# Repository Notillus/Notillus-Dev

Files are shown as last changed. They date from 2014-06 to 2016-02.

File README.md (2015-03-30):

Notillus
========

Repositorio de desarrollo de la Notillus, impresora originalmente inspirada en la Tantillus de https://github.com/Intrinsically-Sublime/Tantillus por su tamaño y portabilidad.

La Notillus ahora lleva el tanga extruder de coleta http://www.thingiverse.com/thing:742584

Los archivos de desarrollo de la Tantillus-Mks ahora estan en: 
https://github.com/darkjavi/Tantillus-MKS

Usando git:

Instrucciones para linux:

-Instalar:

	sudo apt-get install git

-Configurar

	git config --global user.name "TuNombre"

	git config --global user.email "tu@email.com"

-Primer clonado del repo:

	cd carpeta/donde/quieres/descargar

	git clone https://github.com/darkjavi/Notillus.git

-Actualizando el repo:

	cd carpeta/del/repo

	git pull

-Despues de haber modificado cosas en los ficheros:

	cd carpeta/del/repo

	git add .       (añade todos los archivos nuevos)

	git commit -a	(se abrira una ventana en la que obligatoriamente hay que escribir algo sobre los cambios hechos)

	git push origin (manda los cambios de vuelta a github, pedira nombre de usuario/pass)

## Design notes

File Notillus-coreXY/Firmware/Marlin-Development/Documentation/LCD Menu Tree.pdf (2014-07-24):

# Marlin LCD Menu Tree

Main Menu | Tune Menu | Move Menu
Info screen | Main | Prepare
Tune | Speed | Move 10mm | Move Menu
Prepare | Nozzle | Move 1mm | Move axis
Control | Nozzle2 | Move 0.1mm | Move X
Pause print | Nozzle3 | | Move Y
Resume print | Bed | | Move Z
Stop print | Fan speed | Temperature Menu | Extruder
Print from SD | Flow | Control
Change SD card | Babystep X | Nozzle
No SD card | Babystep Y | Nozzle2
Init. SD card | Babystep Z | Nozzle3
| Change filament | Bed
| | Fan speed
| | Autotemp
| Prepare Menu | \002 Min
| Main | \002 Max | Preheat PLA
| Autostart | \002 Fact | Temperature
| Disable steppers | PID-P | Fan speed
| Auto home | PID-I | Nozzle
| Preheat PLA | PID-D | Bed
| Preheat ABS | PID-C | Store memory
| Cooldown | Preheat PLA conf
| Switch power off | Preheat ABS conf | Preheat ABS
Switch power on | Temperature
Move axis | Fan speed
| Motion Menu | Nozzle
| Control | Bed
Control Menu | Z Offset | Store memory
Main | Accel
Temperature | Vxy-jerk
Motion | Vz-jerk
LCD contrast | Ve-jerk
Retract | Vmax x
Store memory | Vmax y
Load memory | Vmax z
Restore failsafe | Vmax e
| Vmin
| VTrav min
SD Card Menu | Amax x
Main | Amax y
Refresh | Amax z
filenames | Amax e
| A-retract
| Xsteps/mm
| Ysteps/mm
| Zsteps/mm
| Esteps/mm
| Endstop abort

Retract Menu
Control
AutoRetr.
Retract mm
Retract F
Hop mm
UnRet +mm
UnRet F

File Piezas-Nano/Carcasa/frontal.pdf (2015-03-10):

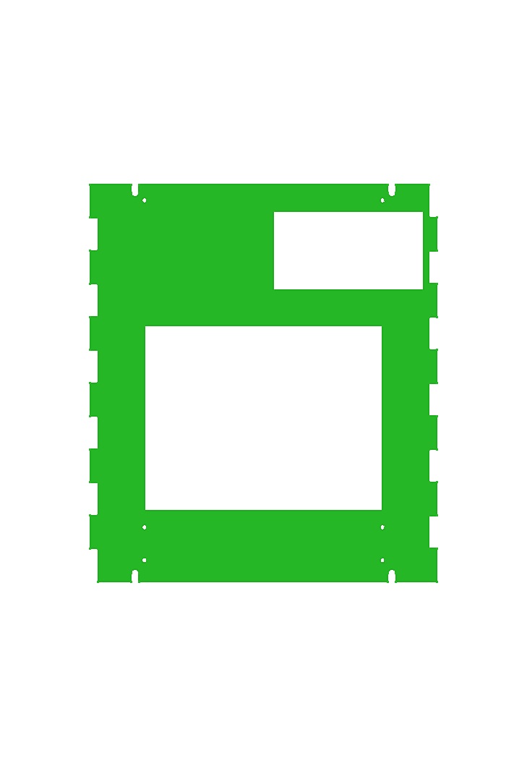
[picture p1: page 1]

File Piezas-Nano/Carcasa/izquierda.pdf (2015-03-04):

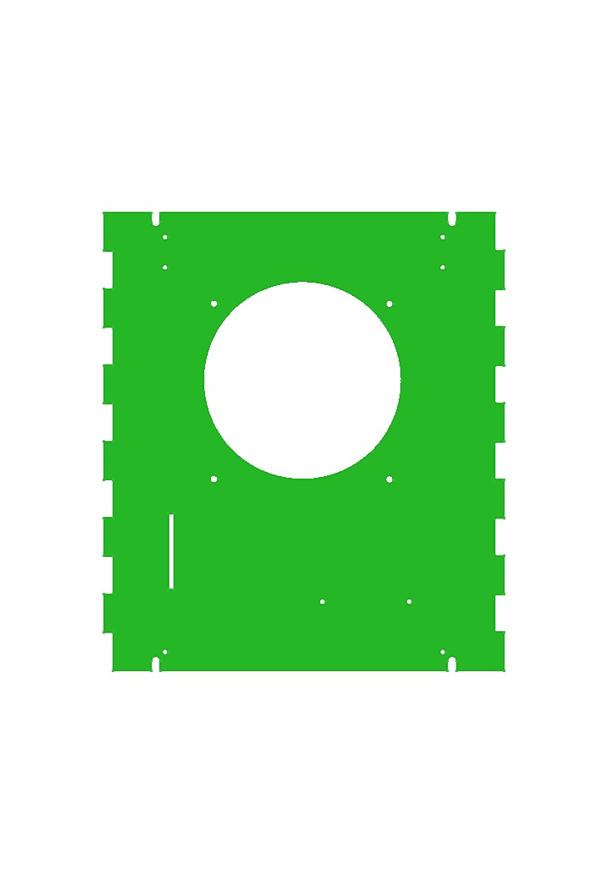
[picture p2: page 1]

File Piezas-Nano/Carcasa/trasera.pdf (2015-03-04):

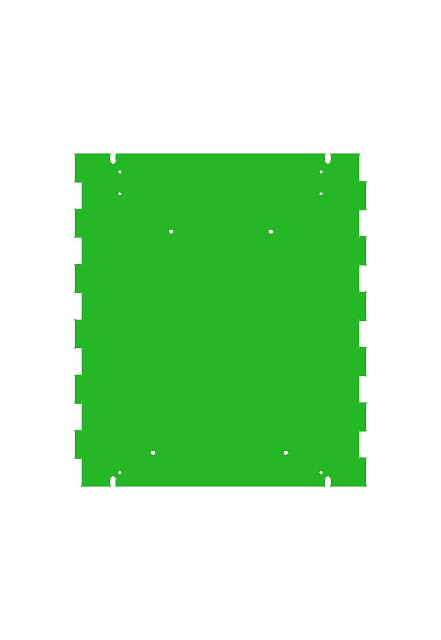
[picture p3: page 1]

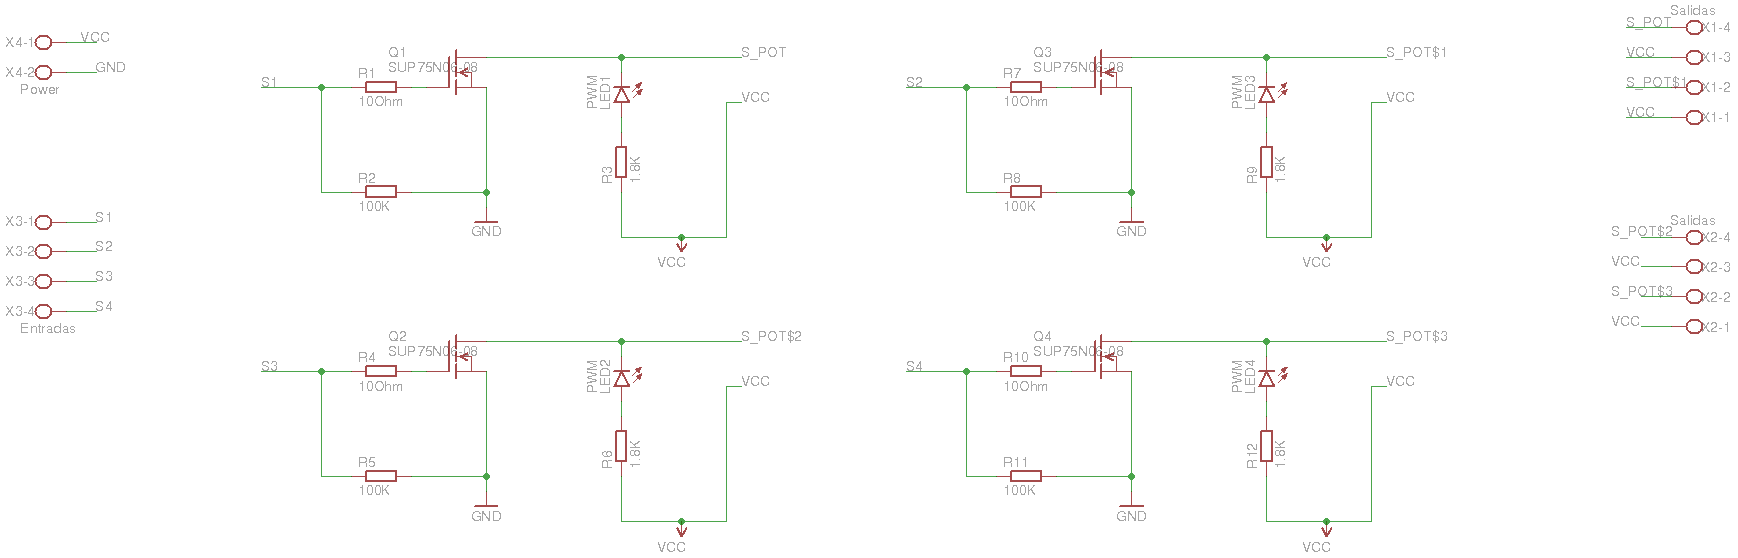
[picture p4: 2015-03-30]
Electronica/ExpansionBoard_sch.png

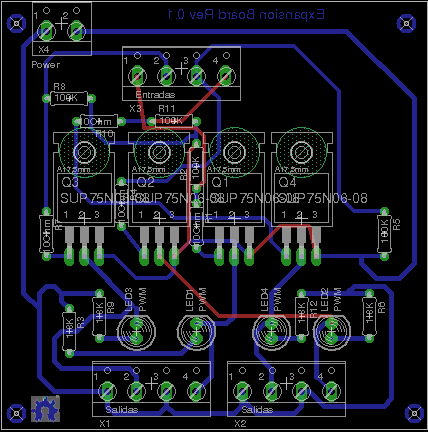
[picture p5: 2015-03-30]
Electronica/ExpansionBoard.png

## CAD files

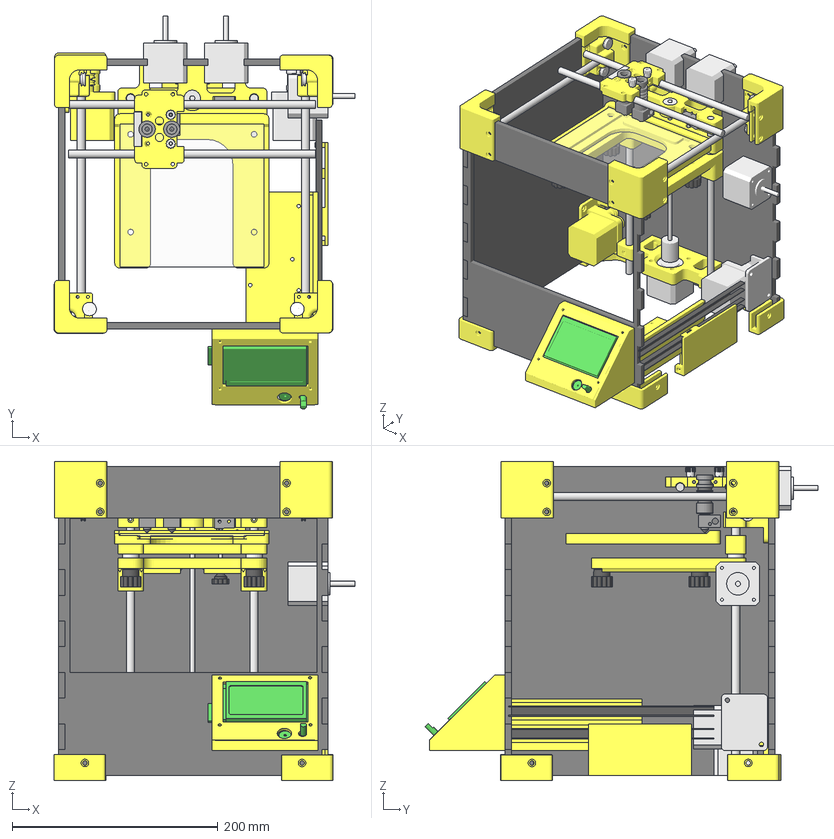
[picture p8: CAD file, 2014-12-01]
Piezas-Javi/Notillus/Ensamblaje1.1.fcstd
292.4 x 382.0 x 310.0 mm
Clone of Pieza base001
Clone of Pieza base003
Varilla8mm002
Clone of Chamfer009
acoplador001
Varilla5mm001
Prism002
PlataformaCierre001
Clone of Chamfer006
enstopz003
LM8UUL002
Nivelador002
625ZZ001
Varilla8mm003
Clone of KnobM007
LM8UUL003
NEMA019
Clone of Chamfer008
Clone of Chamfer007
Cristal001
Plataforna001
Motor
corredera_movil003
corredera_movil004
Completo001
DisplayFull
EsquinaInferior
EsquinaInferior001
EsquinaInferior002
EsquinaInferior003
EsquinaSuperior
EsquinaSuperior001
EsquinaSuperior002
EsquinaSuperior003
JheadMk010
JheadMk011
Knob-ccw002
Knob-cw002
varillax003
varillax002
Fusion001 (Mirror #2)
Fusion004 (Mirror #4)
Fusion002 (Mirror #5)
Cylinder013 (Mirror #6)
Fusion003 (Mirror #7)
Pocket011 (Mirror #9)
Pad027 (Mirror #9)
MotorA
MotorB
NEMA021
NEMA022
NEMA023
compartimento

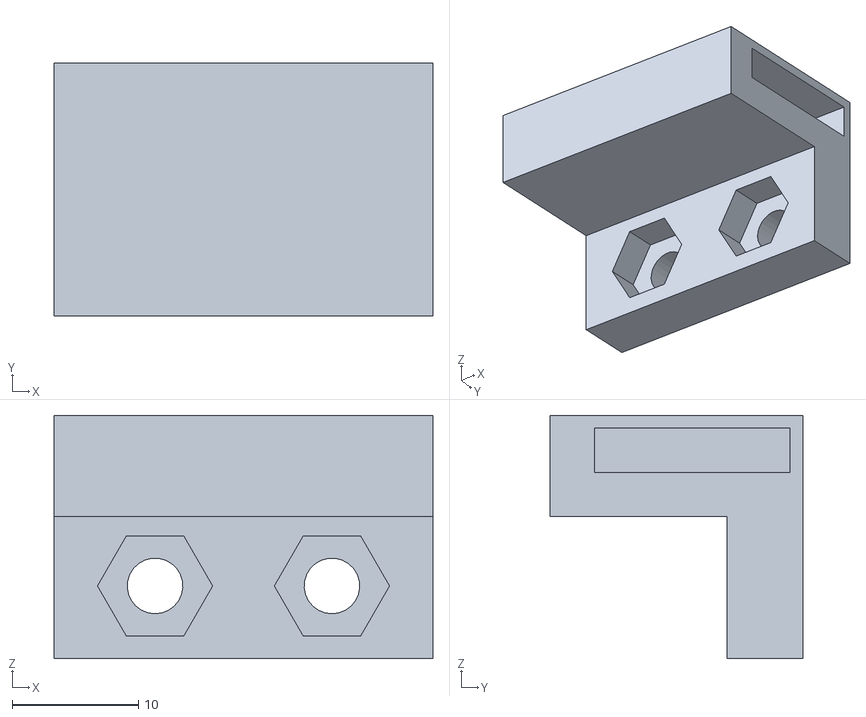
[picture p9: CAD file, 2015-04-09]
Notillus-coreXY/Botiquin/Cierre.stl
30.0 x 20.0 x 19.2

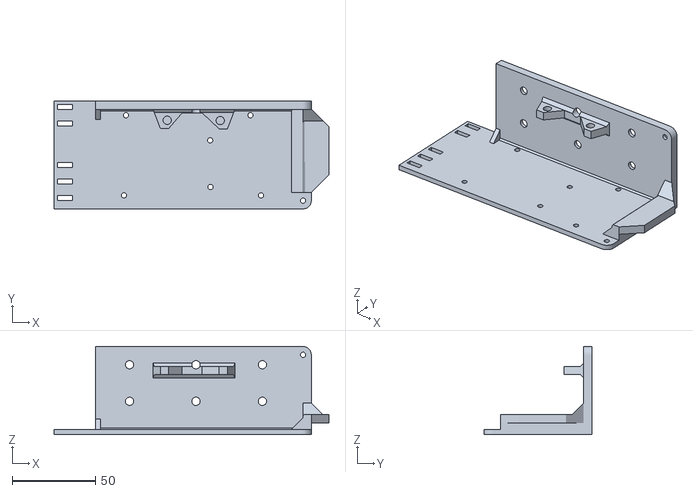
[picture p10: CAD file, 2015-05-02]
Notillus-coreXY/Cajon de Electronica/cajon_electronica.stl
165.6 x 65.0 x 53.0

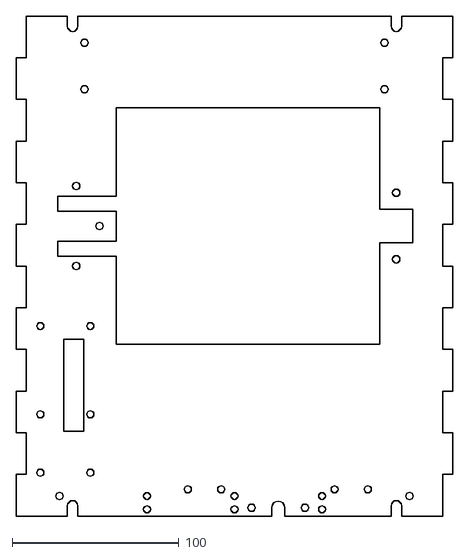
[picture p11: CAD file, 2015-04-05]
Notillus-coreXY/Carcasa/CorteLaser/lateral-izq.dxf
262.0 x 300.0

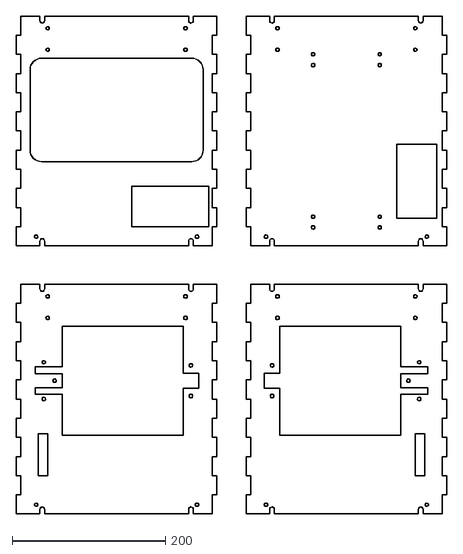
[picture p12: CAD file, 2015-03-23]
Notillus-coreXY/Carcasa/CorteLaser/Pruebas/test.dxf
562.0 x 650.0

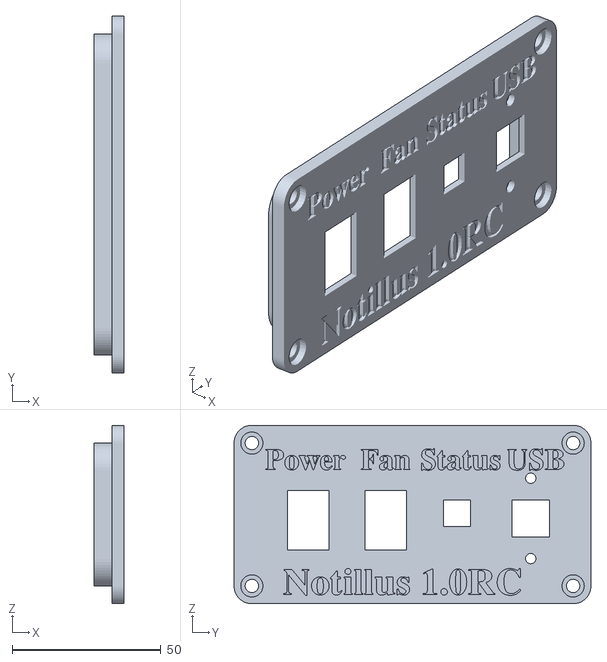
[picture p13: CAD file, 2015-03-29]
Notillus-coreXY/Carcasa/Panel-Interruptores/panel.stl
10.0 x 120.0 x 60.0

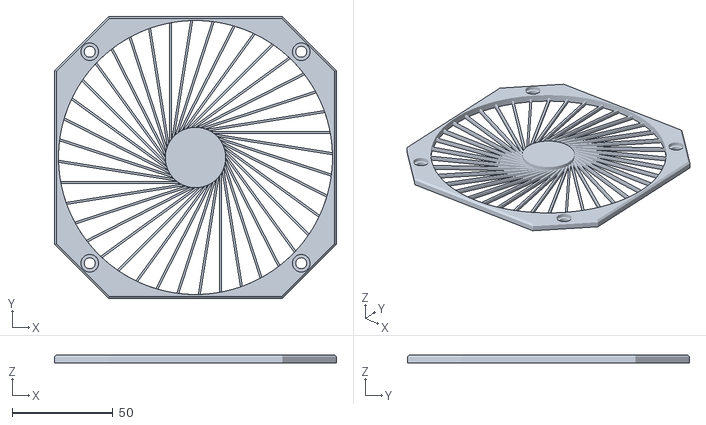
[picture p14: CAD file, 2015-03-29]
Notillus-coreXY/Carcasa/Puerta-Ventis/protector-ventis.stl
140.0 x 140.0 x 4.00

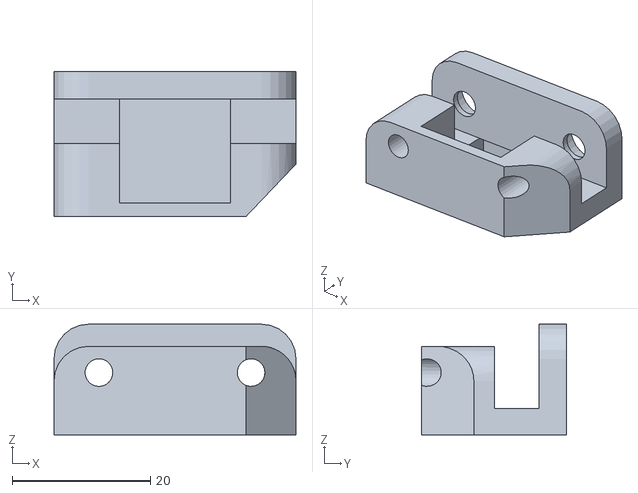
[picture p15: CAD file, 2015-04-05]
Notillus-coreXY/Carcasa/SoporteLeds/soporteBlinkM-trasero.stl
35.0 x 21.0 x 16.0

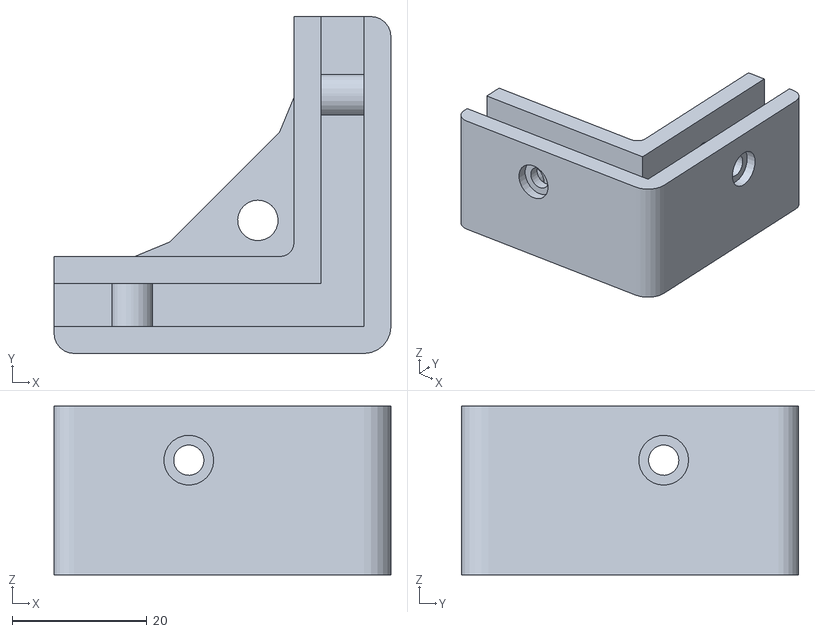
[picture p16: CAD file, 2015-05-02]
Notillus-coreXY/Estructura/esquina-inferior.stl
50.0 x 50.0 x 25.0

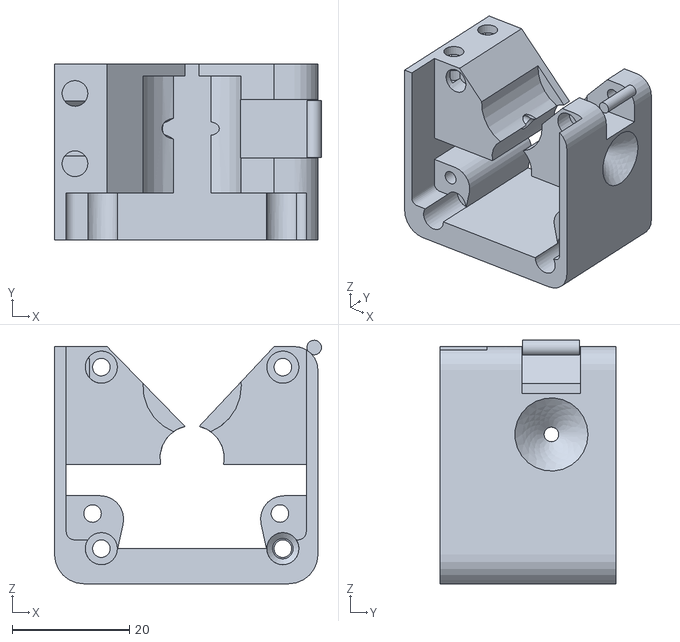
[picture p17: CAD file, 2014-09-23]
Notillus-coreXY/Extrusor/cuerpo.stl
45.6 x 30.0 x 41.6

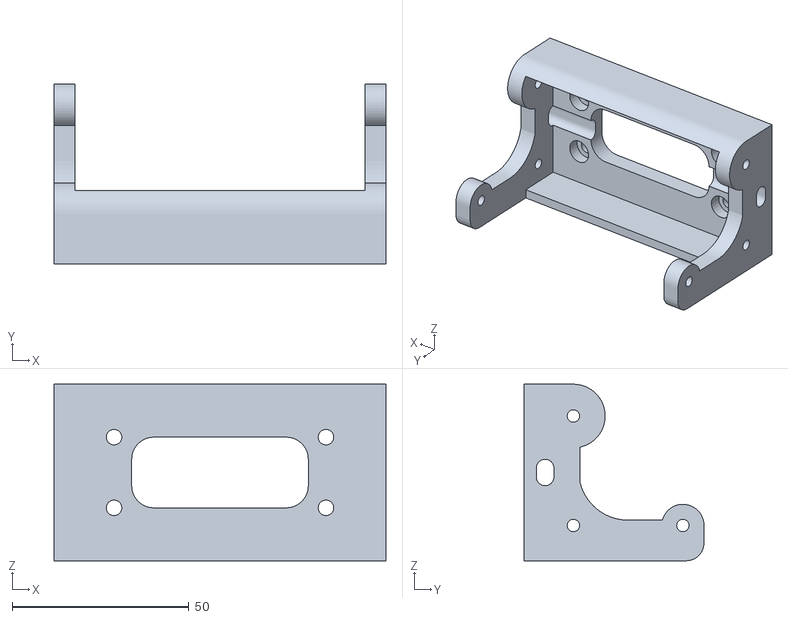
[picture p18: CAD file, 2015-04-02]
Notillus-coreXY/Extrusor/Tanga/soporte.stl
94.0 x 51.0 x 50.0

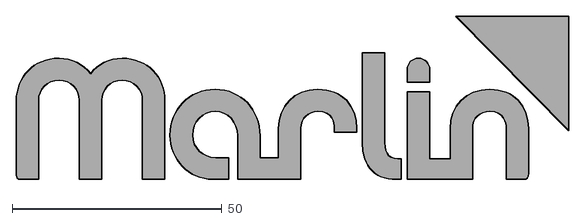
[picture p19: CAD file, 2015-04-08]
Notillus-coreXY/Firmware/Marlin-Development/Documentation/Logo/Marlin Logo.dxf
131.6 x 39.5

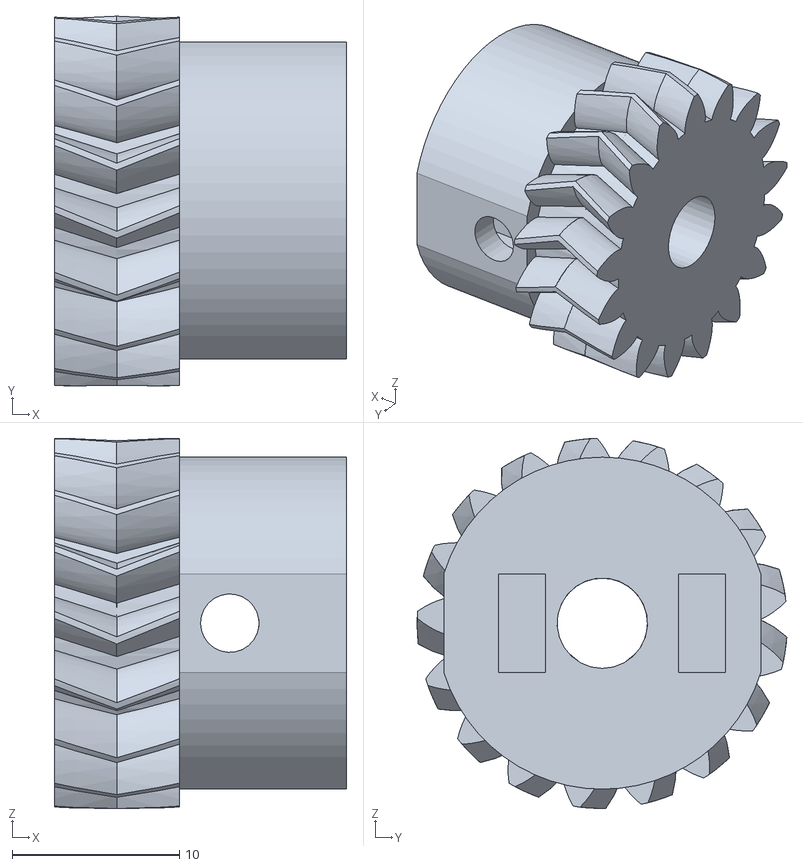
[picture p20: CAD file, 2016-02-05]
Notillus-coreXY/MotoresXY/engranaje-motor-New.stl
17.5 x 22.1 x 22.1

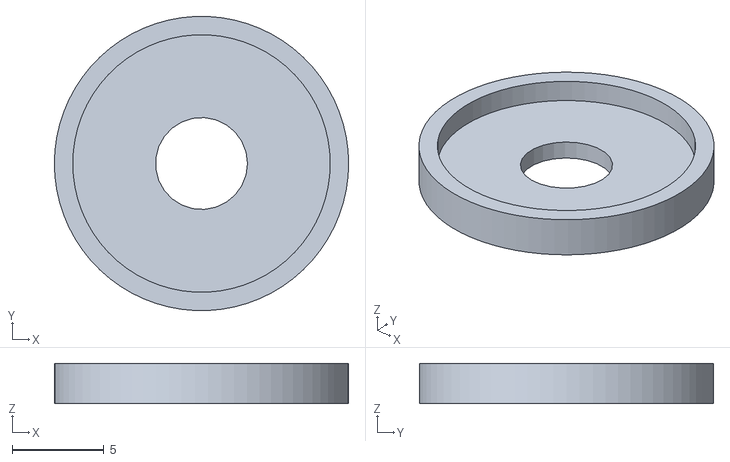
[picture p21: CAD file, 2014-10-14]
Notillus-coreXY/XY/0.6/oreja-polea.stl
16.0 x 16.0 x 2.20

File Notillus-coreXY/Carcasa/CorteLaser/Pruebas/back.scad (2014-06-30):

//Variables de parametrización
h = 300; //alto
w = 250; //ancho
t = 6;	//Grosor


union(){

	cube([w,t,h],center=true);//Frente
	anclaje();//Pestañas de anclaje

}

module anclaje(){
	n = (h/50)/2; 	//Calculo del numero de pestañas
	for (i=[0:n-1]) {  
		translate([w/2,0,-w/2+i*100])  
			cube([20,6,50],center=true);
	
		translate([-w/2,0,-w/2+i*100])  
			cube([20,6,50],center=true);
	}
}

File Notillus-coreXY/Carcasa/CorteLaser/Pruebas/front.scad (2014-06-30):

/**
El volumen interno de los chasis(descontando los salientes de las pestañas de encaje) es de 25x25cm, con 30cm de altura.

Las carcasas de metracrilato se suelen hacer con metracrilato de 6mm de grosor,
*/

//Variables de parametrización
h = 300; //alto
w = 250; //ancho
t = 6;	//Grosor


difference() {  

union(){
	cube([w,t,h],center=true);//Frente
	anclaje();//Pestañas de anclaje

}

//Display

rotate([90,0,0])  
	translate([40,-120,-10])
		cylinder(r=4, h=20, $fn=100); 

translate([0,0,-120])
	cube([50,60,20],center=true);

translate([40,0,-130])
	cube([5,10,5],center=true);


//Ventana
translate([0,0,50])
	cube([150,60,150],center=true);
}

module anclaje(){
	n = (h/50)/2; 	//Calculo del numero de pestañas
	for (i=[0:n-1]) {  
		translate([w/2,0,-w/2+i*100])  
			cube([20,6,50],center=true);
	
		translate([-w/2,0,-w/2+i*100])  
			cube([20,6,50],center=true);
	}
}

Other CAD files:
Notillus-coreXY/XY/carroY-a.stl
Notillus-coreXY/Z/0.6/plataforma-cama.stl
Notillus-coreXY/Z/agrupadas.stl
Piezas-Javi/alineamiento-carcasa-esquinas.fcstd
Notillus-coreXY/Carcasa/CorteLaser/Pruebas/lateral.scad
Notillus-coreXY/Botiquin/Bisagra.stl
Notillus-coreXY/Botiquin/Botiquin.stl
Notillus-coreXY/Cajon de Electronica/Trasera_Display.stl
Notillus-coreXY/Cajon de Electronica/boton_parada.stl
Notillus-coreXY/Cajon de Electronica/puente_display.stl
Notillus-coreXY/Cajon de Electronica/soporte_display.stl
Notillus-coreXY/Carcasa/CorteLaser/Frontal.dxf
Notillus-coreXY/Carcasa/CorteLaser/Pruebas/back.stl
Notillus-coreXY/Carcasa/CorteLaser/Pruebas/front.stl
Notillus-coreXY/Carcasa/CorteLaser/Pruebas/lateral.stl
Notillus-coreXY/Carcasa/CorteLaser/lateral-drcha.dxf
Notillus-coreXY/Carcasa/CorteLaser/trasera.dxf
Notillus-coreXY/Carcasa/Puerta-Ventis/agrupado.stl
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

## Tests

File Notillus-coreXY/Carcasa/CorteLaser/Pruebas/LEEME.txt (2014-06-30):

Aqui iran los ficheros de las versiones Corte con laser/ Mecanizada con la CarveWrigth.

El volumen interno de los chasis(descontando los salientes de las pestañas de encaje) es de 25x25cm, con 30cm de altura.

Las carcasas de metracrilato se suelen hacer con metracrilato de 6mm de grosor, aunque el chasis de pruebas de DM es de 7mm.

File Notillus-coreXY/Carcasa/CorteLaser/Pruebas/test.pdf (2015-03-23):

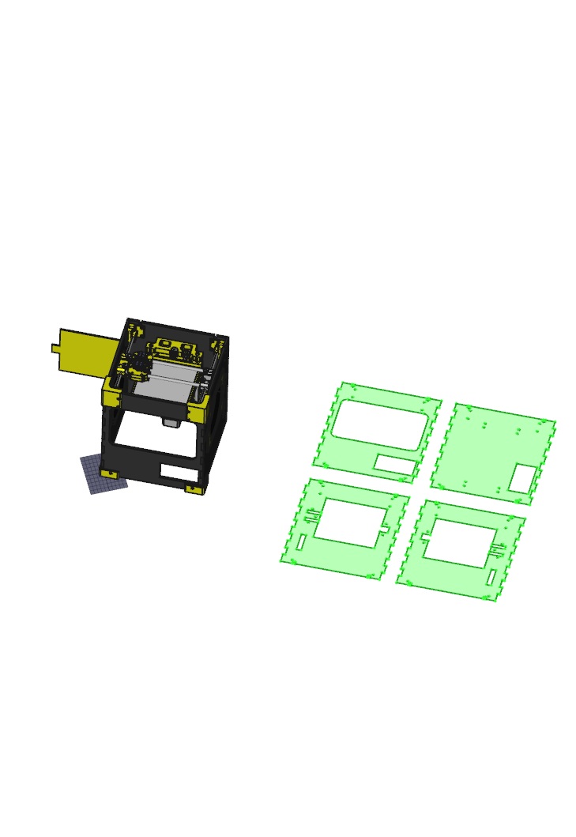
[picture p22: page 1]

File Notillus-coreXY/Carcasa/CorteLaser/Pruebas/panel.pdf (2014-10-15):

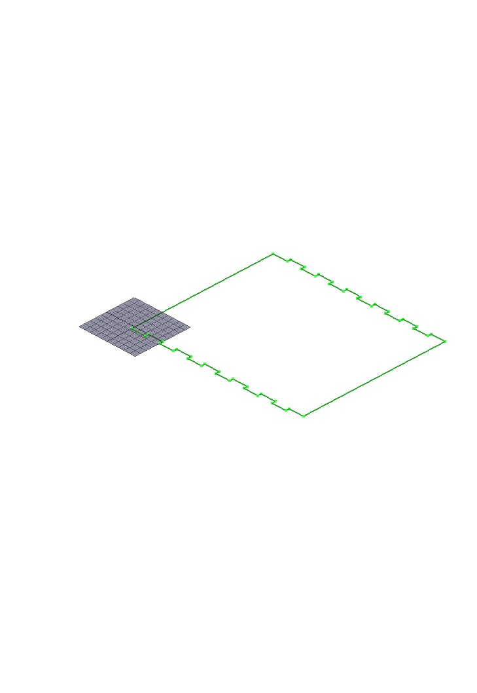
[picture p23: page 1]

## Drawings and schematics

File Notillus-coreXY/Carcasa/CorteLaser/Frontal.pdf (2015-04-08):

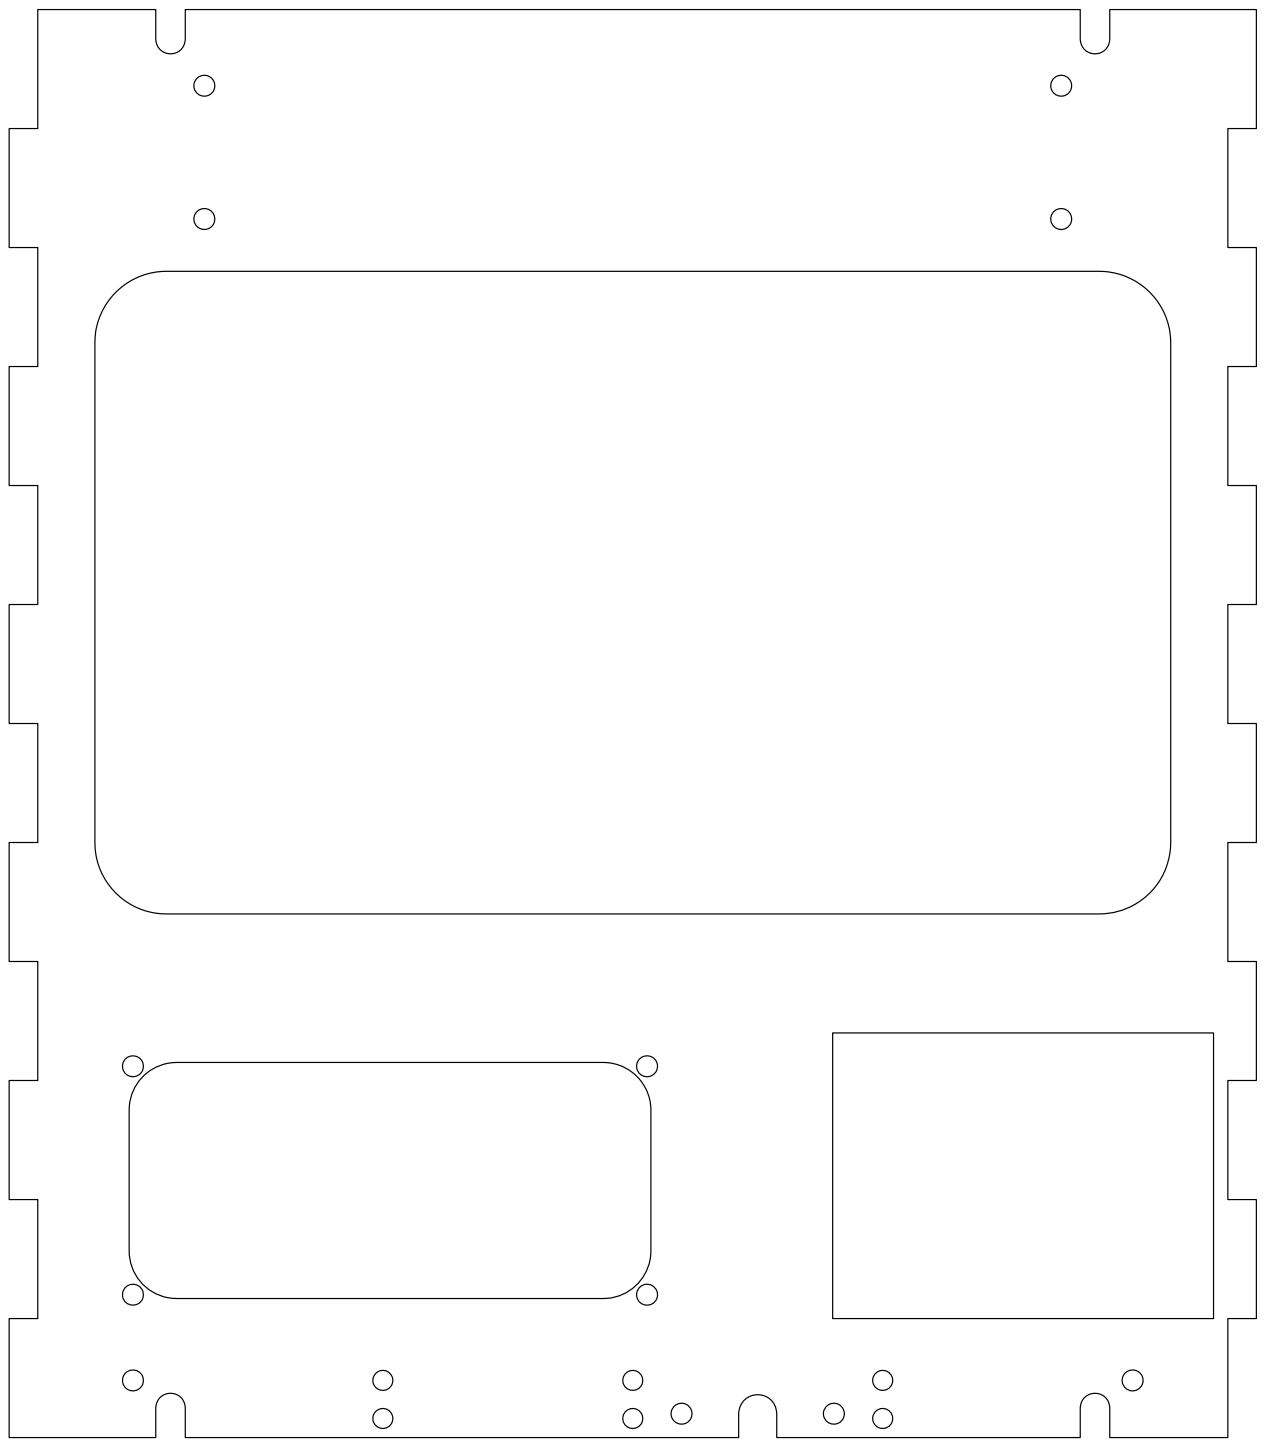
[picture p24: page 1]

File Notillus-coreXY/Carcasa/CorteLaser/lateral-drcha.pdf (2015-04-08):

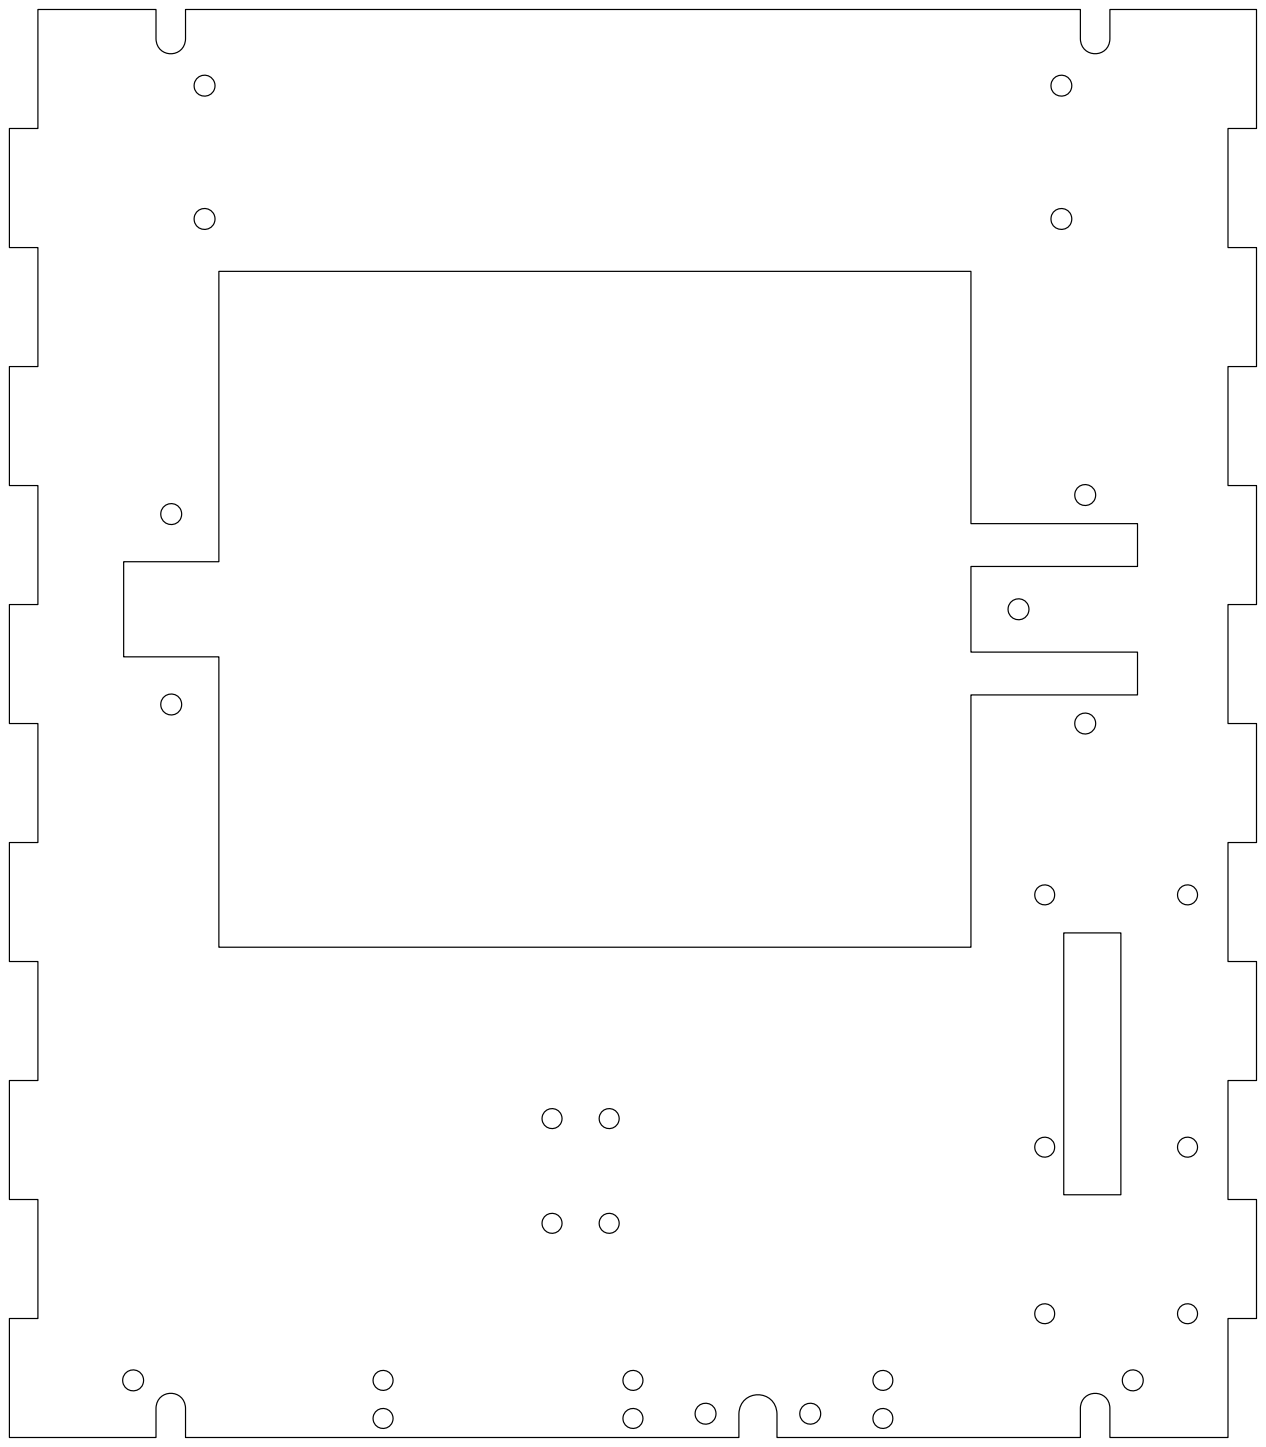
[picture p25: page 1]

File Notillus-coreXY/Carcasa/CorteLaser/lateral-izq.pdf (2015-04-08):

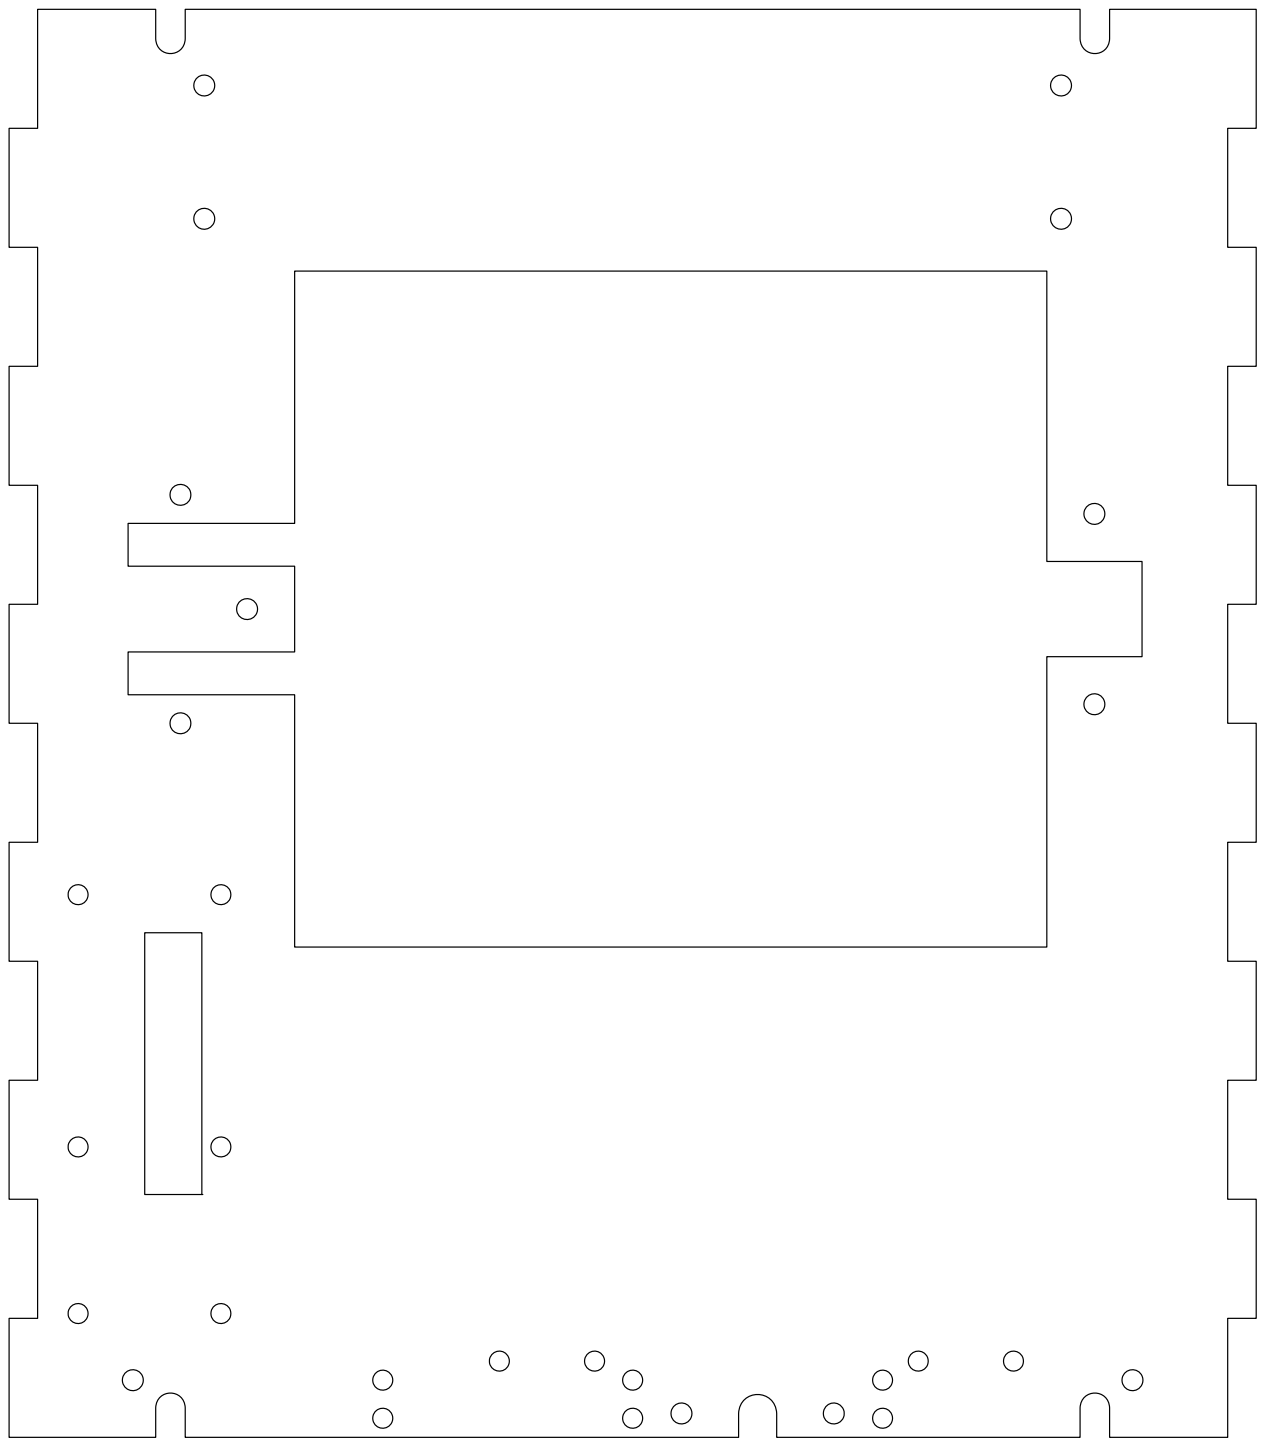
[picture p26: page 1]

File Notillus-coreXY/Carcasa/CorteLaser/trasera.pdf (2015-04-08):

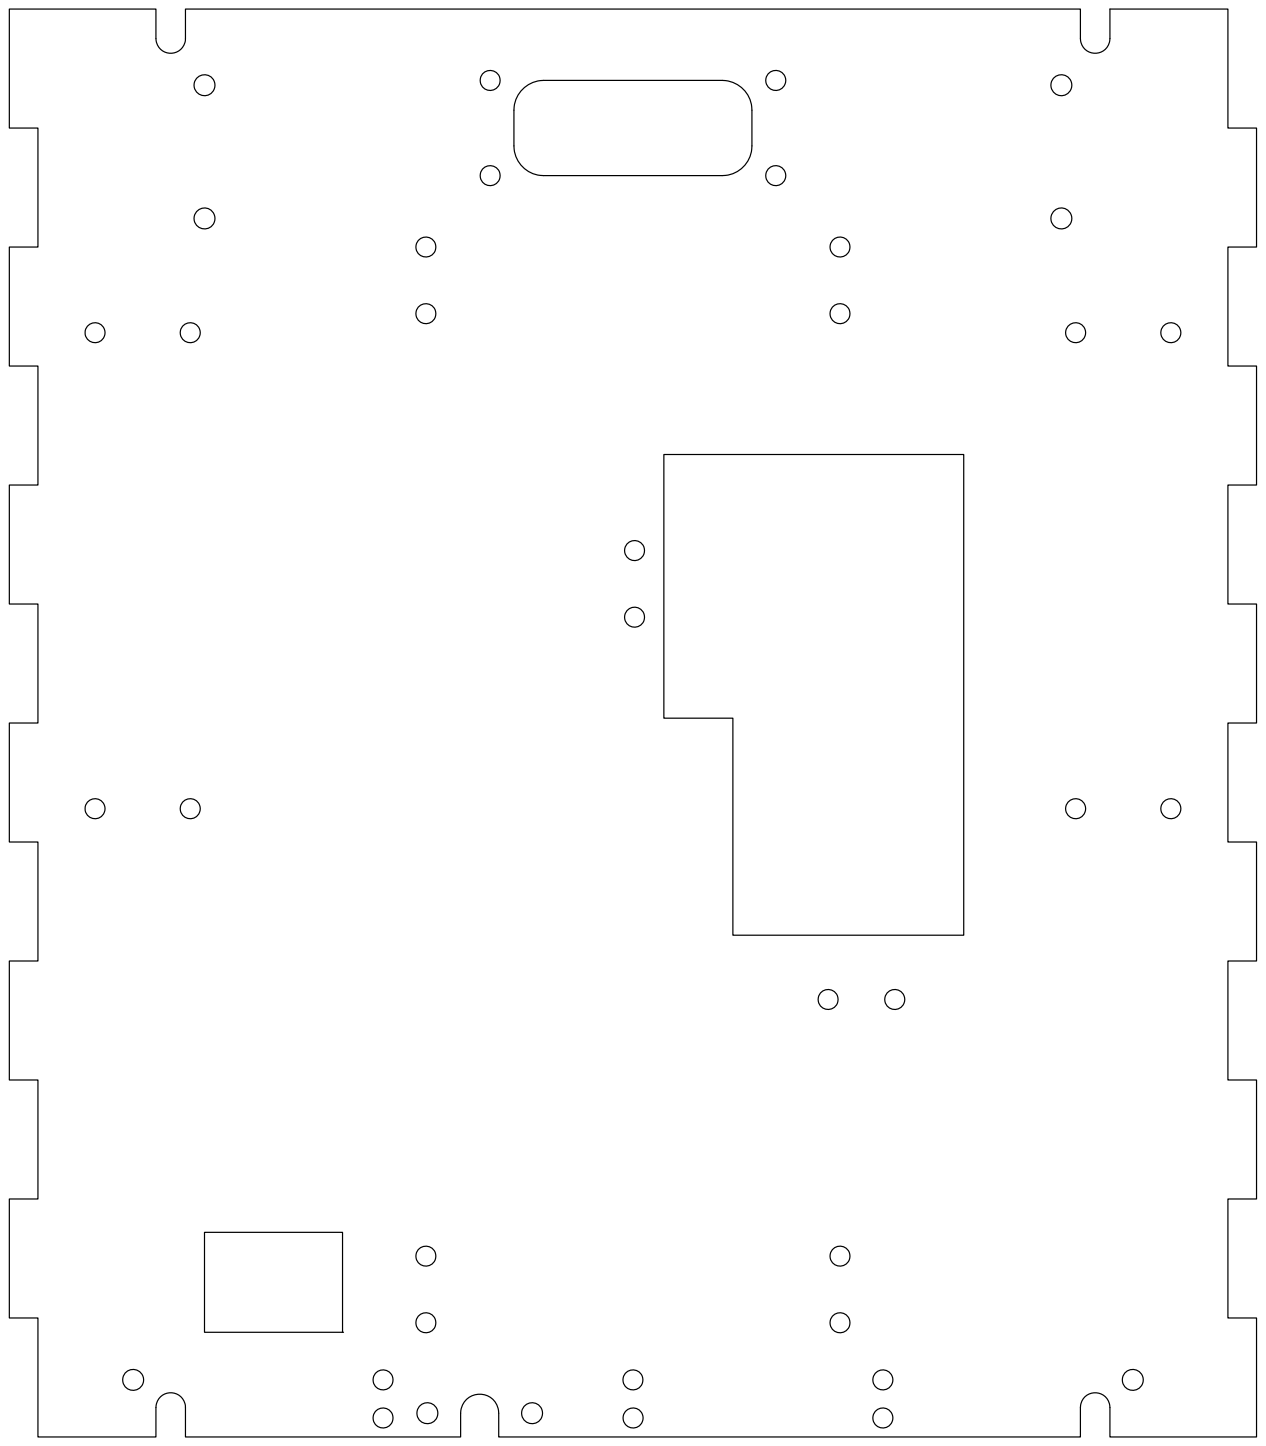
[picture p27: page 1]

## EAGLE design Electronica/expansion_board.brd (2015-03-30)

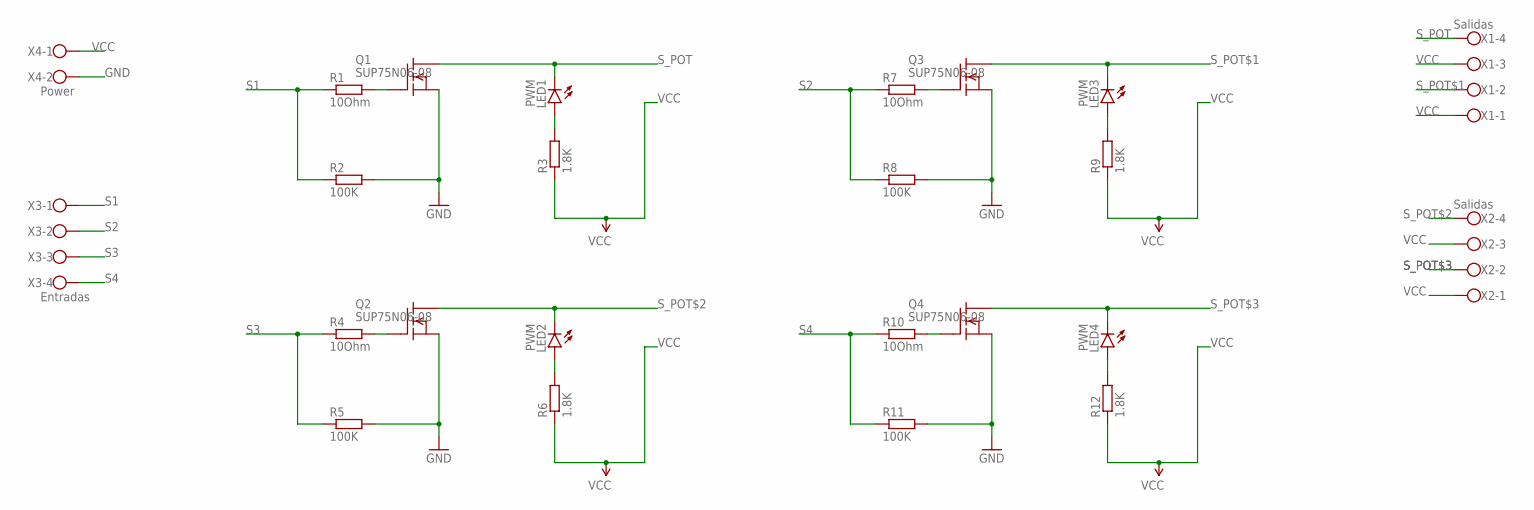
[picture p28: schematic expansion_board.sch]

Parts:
LED1, LED2, LED3, LED4: PWM; LED5MM
Q1, Q2, Q3, Q4: SUP75N06-08; TO220
R1, R4, R7, R10: 10Ohm; 0207/7
R2, R5, R8, R11: 100K; 0207/7
R3, R6, R9, R12: 1.8K; 0207/7
X1, X2: Salidas; W237-4
X3: Entradas; W237-4
X4: Power; W237-102

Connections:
GND: Q1.3 (S), Q2.3 (S), Q3.3 (S), Q4.3 (S), R2.2, R5.2, R8.2, R11.2, X4.2
unnamed: Q3.1 (G), R7.2
unnamed: Q1.1 (G), R1.2
unnamed: Q2.1 (G), R4.2
unnamed: LED1.A, R3.2
unnamed: LED2.A, R6.2
unnamed: LED3.A, R9.2
unnamed: Q4.1 (G), R10.2
unnamed: LED4.A, R12.2
S1: R1.1, R2.1, X3.1
S2: R7.1, R8.1, X3.2
S3: R4.1, R5.1, X3.3
S4: R10.1, R11.1, X3.4
S_POT: LED1.K (C), Q1.2 (D), X1.4
S_POT$1: LED3.K (C), Q3.2 (D), X1.2
S_POT$2: LED2.K (C), Q2.2 (D), X2.4
S_POT$3: LED4.K (C), Q4.2 (D), X2.2
VCC: R3.1, R6.1, R9.1, R12.1, X1.1, X1.3, X2.1, X2.3, X4.1

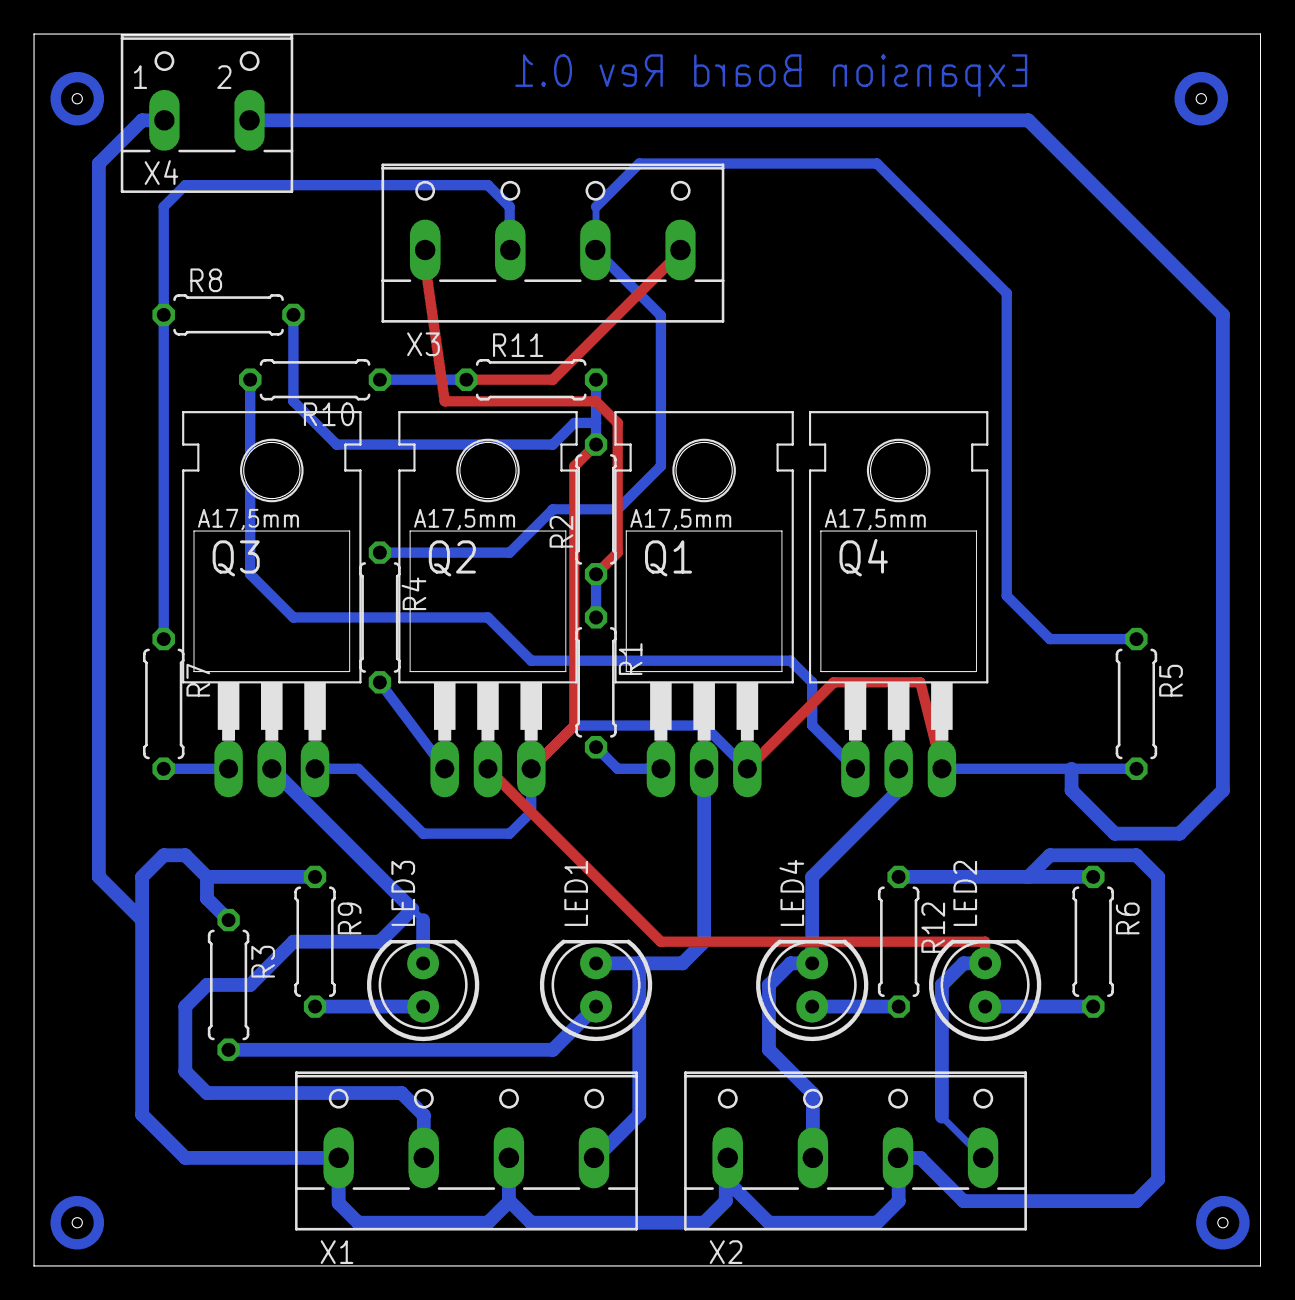
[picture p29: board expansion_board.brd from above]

Board: 2 copper layers, 72.1 x 72.4 mm, 24 parts (0 on the bottom side), 18 nets.

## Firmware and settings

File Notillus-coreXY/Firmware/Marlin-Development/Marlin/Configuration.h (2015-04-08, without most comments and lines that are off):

#define CONFIGURATION_H
#include "boards.h"
#define STRING_VERSION_CONFIG_H __DATE__ " " __TIME__ // build date and time
#define STRING_CONFIG_H_AUTHOR "(none, default config)" // Who made the changes.
#define SERIAL_PORT 0
#define BAUDRATE 115200
  #define MOTHERBOARD 36
#define CUSTOM_MENDEL_NAME "Notillus 0.9"
#define EXTRUDERS 1
#define POWER_SUPPLY 1
#define TEMP_SENSOR_0 5
#define TEMP_SENSOR_1 0
#define TEMP_SENSOR_2 0
#define TEMP_SENSOR_BED 0
#define MAX_REDUNDANT_TEMP_SENSOR_DIFF 10
#define TEMP_RESIDENCY_TIME 10  // (seconds)
#define TEMP_HYSTERESIS 3       // (degC) range of +/- temperatures considered "close" to the target one
#define TEMP_WINDOW     1       // (degC) Window around target to start the residency timer x degC early.
#define HEATER_0_MINTEMP 5
#define HEATER_1_MINTEMP 5
#define HEATER_2_MINTEMP 5
#define BED_MINTEMP 5
#define HEATER_0_MAXTEMP 260
#define HEATER_1_MAXTEMP 260
#define HEATER_2_MAXTEMP 260
#define BED_MAXTEMP 150
#define PIDTEMP
#define BANG_MAX 255 // limits current to nozzle while in bang-bang mode; 255=full current
#define PID_MAX BANG_MAX // limits current to nozzle while PID is active (see PID_FUNCTIONAL_RANGE below); 255=full current
  #define PID_FUNCTIONAL_RANGE 10 // If the temperature difference between the target temperature and the actual temperature
  #define PID_INTEGRAL_DRIVE_MAX PID_MAX  //limit for the integral term
  #define K1 0.95 //smoothing factor within the PID
  #define PID_dT ((OVERSAMPLENR * 10.0)/(F_CPU / 64.0 / 256.0)) //sampling period of the temperature routine
    #define  DEFAULT_Kp 22.2
    #define  DEFAULT_Ki 1.08
    #define  DEFAULT_Kd 114
#define MAX_BED_POWER 255 // limits duty cycle to bed; 255=full current
#define PREVENT_DANGEROUS_EXTRUDE
#define PREVENT_LENGTHY_EXTRUDE
#define EXTRUDE_MINTEMP 150
#define EXTRUDE_MAXLENGTH (X_MAX_LENGTH+Y_MAX_LENGTH) //prevent extrusion of very large distances.
#define THERMAL_RUNAWAY_PROTECTION_PERIOD 40 //in seconds
#define THERMAL_RUNAWAY_PROTECTION_HYSTERESIS 4 // in degree Celsius
#define COREXY
#define ENDSTOPPULLUPS // Comment this out (using // at the start of the line) to disable the endstop pullup resistors
  #define ENDSTOPPULLUP_XMAX
  #define ENDSTOPPULLUP_YMAX
  #define ENDSTOPPULLUP_ZMAX
  #define ENDSTOPPULLUP_XMIN
  #define ENDSTOPPULLUP_YMIN
  #define ENDSTOPPULLUP_ZMIN
const bool X_MIN_ENDSTOP_INVERTING = false; // set to true to invert the logic of the endstop.
const bool Y_MIN_ENDSTOP_INVERTING = false; // set to true to invert the logic of the endstop.
const bool Z_MIN_ENDSTOP_INVERTING = false; // set to true to invert the logic of the endstop.
const bool X_MAX_ENDSTOP_INVERTING = true; // set to true to invert the logic of the endstop.
const bool Y_MAX_ENDSTOP_INVERTING = true; // set to true to invert the logic of the endstop.
const bool Z_MAX_ENDSTOP_INVERTING = true; // set to true to invert the logic of the endstop.
#if defined(COREXY) && !defined(DISABLE_MAX_ENDSTOPS)
  #define DISABLE_MAX_ENDSTOPS
#endif
#define X_ENABLE_ON 0
#define Y_ENABLE_ON 0
#define Z_ENABLE_ON 0
#define E_ENABLE_ON 0 // For all extruders
#define DISABLE_X false
#define DISABLE_Y false
#define DISABLE_Z false
#define DISABLE_E false // For all extruders
#define DISABLE_INACTIVE_EXTRUDER true //disable only inactive extruders and keep active extruder enabled
#define INVERT_X_DIR false    // for Mendel set to false, for Orca set to true
#define INVERT_Y_DIR false    // for Mendel set to true, for Orca set to false
#define INVERT_Z_DIR false     // for Mendel set to false, for Orca set to true
#define INVERT_E0_DIR true   // for direct drive extruder v9 set to true, for geared extruder set to false
#define INVERT_E1_DIR true    // for direct drive extruder v9 set to true, for geared extruder set to false
#define INVERT_E2_DIR false   // for direct drive extruder v9 set to true, for geared extruder set to false
#define X_HOME_DIR -1
#define Y_HOME_DIR -1
#define Z_HOME_DIR -1
#define min_software_endstops true // If true, axis won't move to coordinates less than HOME_POS.
#define max_software_endstops true  // If true, axis won't move to coordinates greater than the defined lengths below.
#define X_MAX_POS 120
#define X_MIN_POS 0
#define Y_MAX_POS 120
#define Y_MIN_POS 0
#define Z_MAX_POS 95
#define Z_MIN_POS 0
#define X_MAX_LENGTH (X_MAX_POS - X_MIN_POS)
#define Y_MAX_LENGTH (Y_MAX_POS - Y_MIN_POS)
#define Z_MAX_LENGTH (Z_MAX_POS - Z_MIN_POS)
#define Z_PROBE_REPEATABILITY_TEST  // If not commented out, Z-Probe Repeatability test will be included if Auto Bed Leveling is Enabled.
#define MANUAL_X_HOME_POS 0
#define MANUAL_Y_HOME_POS 0
#define MANUAL_Z_HOME_POS 0
#define NUM_AXIS 4 // The axis order in all axis related arrays is X, Y, Z, E
#define HOMING_FEEDRATE {60*60, 60*60, 4*60, 0}  // set the homing speeds (mm/min)
#define DEFAULT_AXIS_STEPS_PER_UNIT   {84.38,84.38,4020,85}  // default steps per unit for Ultimaker
#define DEFAULT_MAX_FEEDRATE          {500, 500, 4, 60}    // (mm/sec)
#define DEFAULT_MAX_ACCELERATION      {9000,9000,100,10000}    // X, Y, Z, E maximum start speed for accelerated moves. E default values are good for Skeinforge 40+, for older versions raise them a lot.
#define DEFAULT_ACCELERATION          2500    // X, Y, Z and E max acceleration in mm/s^2 for printing moves
#define DEFAULT_RETRACT_ACCELERATION  3500   // X, Y, Z and E max acceleration in mm/s^2 for retracts
#define DEFAULT_XYJERK                20.0    // (mm/sec)
#define DEFAULT_ZJERK                 0.4     // (mm/sec)
#define DEFAULT_EJERK                 5.0    // (mm/sec)
#define CUSTOM_M_CODES
  #define CUSTOM_M_CODE_SET_Z_PROBE_OFFSET 851
  #define Z_PROBE_OFFSET_RANGE_MIN -15
  #define Z_PROBE_OFFSET_RANGE_MAX -5
#define EEPROM_SETTINGS
#define EEPROM_CHITCHAT
#define PLA_PREHEAT_HOTEND_TEMP 180
#define PLA_PREHEAT_HPB_TEMP 0
#define PLA_PREHEAT_FAN_SPEED 128   // Insert Value between 0 and 255
#define ABS_PREHEAT_HOTEND_TEMP 220
#define ABS_PREHEAT_HPB_TEMP 0
#define ABS_PREHEAT_FAN_SPEED 255   // Insert Value between 0 and 255
#define REPRAP_DISCOUNT_FULL_GRAPHIC_SMART_CONTROLLER
 #define DOGLCD
 #define U8GLIB_ST7920
 #define REPRAP_DISCOUNT_SMART_CONTROLLER
 #define ULTIPANEL
 #define NEWPANEL
  #define SDSUPPORT
  #define ULTRA_LCD
    #define LCD_WIDTH 20
    #define LCD_HEIGHT 5
#  define DEFAULT_LCD_CONTRAST 32
#define SOFT_PWM_SCALE 0
#define FILAMENT_SENSOR_EXTRUDER_NUM	0  //The number of the extruder that has the filament sensor (0,1,2)
#define MEASUREMENT_DELAY_CM			14  //measurement delay in cm.  This is the distance from filament sensor to middle of barrel
#define DEFAULT_NOMINAL_FILAMENT_DIA  3.0  //Enter the diameter (in mm) of the filament generally used (3.0 mm or 1.75 mm) - this is then used in the slicer software.  Used for sensor reading validation
#define MEASURED_UPPER_LIMIT          3.30  //upper limit factor used for sensor reading validation in mm
#define MEASURED_LOWER_LIMIT          1.90  //lower limit factor for sensor reading validation in mm
#define MAX_MEASUREMENT_DELAY			20  //delay buffer size in bytes (1 byte = 1cm)- limits maximum measurement delay allowable (must be larger than MEASUREMENT_DELAY_CM  and lower number saves RAM)
#define DEFAULT_MEASURED_FILAMENT_DIA  DEFAULT_NOMINAL_FILAMENT_DIA  //set measured to nominal initially
#include "Configuration_adv.h"
#include "thermistortables.h"

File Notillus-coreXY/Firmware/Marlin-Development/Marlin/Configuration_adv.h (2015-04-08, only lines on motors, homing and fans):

#define CONTROLLERFAN_PIN -1 //Pin used for the fan to cool controller (-1 to disable)
#define EXTRUDER_0_AUTO_FAN_PIN   -1
#define EXTRUDER_1_AUTO_FAN_PIN   -1
#define EXTRUDER_2_AUTO_FAN_PIN   -1
#define ENDSTOPS_ONLY_FOR_HOMING // If defined the endstops will only be used for homing
#define X_HOME_RETRACT_MM 3
#define Y_HOME_RETRACT_MM 3
#define Z_HOME_RETRACT_MM 1.5
#define MICROSTEP1 LOW,LOW
#define MICROSTEP2 HIGH,LOW
#define MICROSTEP4 LOW,HIGH
#define MICROSTEP8 HIGH,HIGH
#define MICROSTEP16 HIGH,HIGH
#define MICROSTEP_MODES {16,16,16,16,16} // [1,2,4,8,16]
#define DIGIPOT_MOTOR_CURRENT {135,135,135,135,135} // Values 0-255 (RAMBO 135 = ~0.75A, 185 = ~1A)
#define DIGIPOT_I2C_MOTOR_CURRENTS {1.0, 1.0, 1.0, 1.0, 1.0, 1.0, 1.0, 1.0}

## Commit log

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2014-06-28 Carpetas recolocadas. Primera recopilacion de las piezas para el kit de tantillusmks Faltan muchas cosas por ordenar
    [Endstop_holder.stl, carro-hotend.stl, knob_fixed.stl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]
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2014-06-30 Versión alpha del chasis. Sin agujeros de anclaje ¡Las medidas del display hay que contrastarlas!
    [back.scad, back.stl, front.scad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]
2014-06-30 versión alpha del frontal Sin agujeros de anclaje ¡¡Las medidas del display no son reales!!
    [front.scad]
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2014-07-31 Nuevo y mejorado barrilete para el hilo. 88 pasos por mm Firmware configurado para la version rslot de hilo con barilletes
    modified: Kit-TantillusMks-TSLOT/Extras/spectra-reel-m8-v2.stl
    modified: Kit-TantillusMks-TSLOT/Firmware/Marlin-tantillus-Moebyus/Marlin/Configuration.h
    modified: Piezas-Javi/Tantillus/spectra-reel-8mm-smaller2.fcstd
    renamed: Piezas-Javi/Tantillus/spectra-reel-8mm-smaller2.fcstd -> Piezas-Javi/Tantillus/spectra-reel-8mm-smaller2.fcstd1
    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
    [Configuration.h, spectra-reel-8mm-smaller2.fcstd, spectra-reel-m8-v2.stl]
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2014-08-05 version 0.8 del soporte de filamento para la TSLOT new file: Piezas-Javi/Tantillus/soporte-filamento-pieza2.fcstd new file: Piezas-Javi/Tantillus/soporte-filamento-pieza2.fcstd1 new file: Piezas-Javi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
    [soporte-filamento-pieza2.fcstd, soporte-filamento-pieza3.fcstd, soporte-filamento.fcstd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]
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2014-08-08 Añadido cajon para electrónica (ATENCION!! MEDIDAS NO REALES!) Añadido cajonera para electrónica (ATENCION!! MEDIDAS NO REALES!) Añadido soporte para ventilación de electrónica
    [RAMPS_Fan_Mount.scad, RAMPS_Fan_Mount.stl, cajon-electronica.fcstd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]
2014-08-09 Empezados los esquinazos y las piezas de cruce del hilo
    new file: Piezas-Javi/Notillus/corexy-cruce-alineado.fcstd
    new file: Piezas-Javi/Notillus/esquina.fcstd
    [corexy-cruce-alineado.fcstd, esquina.fcstd]
2014-08-11 Piezas del coreXY, falta ajustar la medida de las poleas del hilo
    new file: Piezas-Javi/Notillus/coreXY-carroY.fcstd
    new file: Piezas-Javi/Notillus/coreXY-frontal.fcstd
    new file: Piezas-Javi/Notillus/coreXY-trasera.fcstd
    [coreXY-carroY.fcstd, coreXY-frontal.fcstd, coreXY-trasera.fcstd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]
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2014-08-16 new file: Notillus-coreXY/STL/esquinas-superiores.stl modified: Piezas-Javi/Notillus/esquina-superior.fcstd modified: Piezas-Javi/Notillus/esquina-superior.fcstd1 new file: Piezas-Javi/Notillus/esqui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
    [esquina-superior.fcstd, esquina-superior2.fcstd, esquinas-superiores.stl]
2014-08-16 Pieza core-frontal lista ; Tiempo estimado de impresion : 1:30 la pareja
    pieza core-trasera casi lista, falta la alineacion vertical.
    new file: Notillus-coreXY/STL/XY/corexy-frontal-both.stl
    modified: Piezas-Javi/Notillus/coreXY-frontal.fcstd
    modified: Piezas-Javi/Notillus/coreXY-trasera.fcstd
    [core-frontal.stl, coreXY-frontal.fcstd, coreXY-trasera.fcstd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]
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2014-08-16 Añadido frontal para el display Añadido rueda para el encoder del display Prototipo del cajon para electronica [¡COMPROBAR MEDIDAS!]
    [RAMPS_Fan_Mount.scad, RAMPS_Fan_Mount.stl, cajon-electronica.fcstd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]
2014-08-16 Arreglado el comit erroneo
    No se muy bien como reorganice los ficheros en el equipo de la lulzbot y se borraron las carpetas del chasis
    [Endstop_holder.stl, back.scad, back.stl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]
2014-08-16 Primera version de la pieza corexy-trasera. Imprime bien, aunque el final del carrera le queda un poco justo
    new file: Notillus-coreXY/XY/corexy-trasera.stl
    [coreXY-frontal.fcstd, coreXY-trasera.fcstd, corexy-trasera.stl]
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2014-08-19 Incluido espacio para la pata en el soporte de motor con esquina.
    [soporte-Nema-Esquina.fcstd]
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2014-08-20 Nuevo molde para hacer las patas de silicona new file: Notillus-coreXY/Estructura/molde-patas.stl new file: Piezas-Javi/Tantillus/Molde-patas.fcstd
    [Molde-patas.fcstd, molde-patas.stl]
2014-08-20 Version 3.1 de la guia de hilo Version 2.0 del soporte motor
    [esquina.stl, guia-hilo.fcstd, guia-hilo_v2_2.fcstd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]
2014-08-21 carro x : pieza empezada soporte de motor achaflanado , tiempo estimado de impresion 1:45 new file: Piezas-Javi/Notillus/coreXY-carroX.fcstd new file: Piezas-Nano/soporte-Nema_v2-achaflanado.fcstd
    [coreXY-carroX.fcstd, soporte-Nema_v2-achaflanado.fcstd]
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2014-08-21 carro x progresa adecuadamente new file: Notillus-coreXY/Estructura/soporte-motor.stl new file: Notillus-coreXY/XY/corexy-carroX.stl modified: Piezas-Javi/Notillus/coreXY-carroX.fcstd
    [coreXY-carroX.fcstd, corexy-carroX.stl, soporte-motor.stl]
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2014-09-02 Barriletes modificados Soporte para ventilador de capa Rieles de cajon [SIN MEDIDAS REALES]
    [barrilete_v3.fcstd, barrilete_v3.stl, rieles.fcstd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]
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2014-09-06 Enredando con el firmware para activar el ventilador de capa y cambiar el logo/textos de la pantalla de inicio. en add --all se han metido algunos ficheros antiguos que supongo que no se habian añadi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
    [Z_upper.stl, coreXY-tensor.fcstd, corexy-tensor.stl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]
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

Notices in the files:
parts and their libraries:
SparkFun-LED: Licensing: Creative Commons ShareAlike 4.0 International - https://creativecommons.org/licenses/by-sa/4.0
